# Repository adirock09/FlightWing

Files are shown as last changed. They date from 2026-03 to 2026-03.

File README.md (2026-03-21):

# FlightWing
Screenshot (177)
I made a custom Flight Controller which controls 3 Servos and 1 Escs which is based on an STM32 chip , it has 6 channel input available so it can be connected to a receiver and has a microSD Card, battery charger , IMU and Pressure Sensor . It has a USB-C for uploading code and charging purpose.

## Features

- Based on STM32 Chip
- 2-layer compact PCB
- USB connection for programming and power
- Onboard 3.3V and 5V voltage regulation
- Compact footprint for small projects
- IMU and Pressure Sensor<br>
- 
- ## Bill of Materials (BOM)
| Serial Num | Description | Total (USD) | 
|----:|---|---|
| 1  | PCB and Assembly  |77.86 |
| 2 | Shipping JLCPCB  |14.51 |

<br>
### 💰 Cost Summary

- **Estimated Total Cost ( PCB ASSEMBLY + Shipping):** **$92.37	 USD**
-  ## Schematic & PCB<br>
Screenshot (181)<br>
Screenshot (176)<br>

## 3d Render<br>
Screenshot (177)<br>
Screenshot (178)<br>

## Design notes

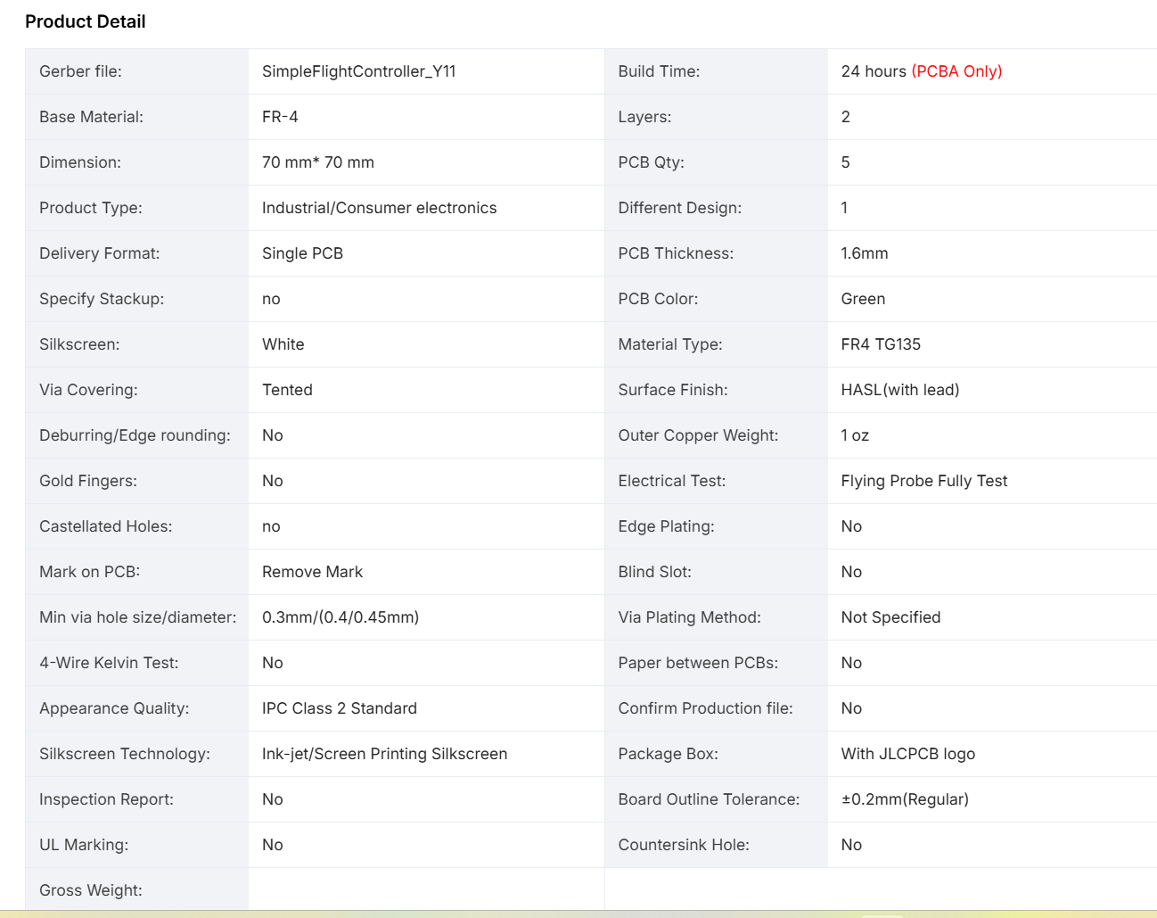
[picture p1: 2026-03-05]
options for PCBA.png

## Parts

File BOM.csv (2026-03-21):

Item | Price | Source
PCB and Assembly | 77.86 | JLCPCB
Shipping JLCPCB | 14.51 | JLCPCB
Total | 92.37 | JLCPCB

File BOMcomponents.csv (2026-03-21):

Designator | Footprint | Quantity | Value | LCSC Part #
BOOT, RESET | SW-SMD_L3.9-W3.0-P4.45 | 2 | TS-1088-AR02016 | C720477
C1, C28, C29, C30 | 0402 | 4 | 1uF
C10, C11, C13 | 0805 | 3 | 22uF
C12, C2, C9 | 0603 | 3 | 10uF
C14, C15, C19, C20, C21, C22, C23, C24, C25, C26, C27, C37 | 0201 | 12 | 100nF
C16 | 0603 | 1 | 2.2uF
C17, C18 | 0402 | 2 | 22uF
C3, C31, C5 | 0402 | 3 | 10uF
C32 | 0201 | 1 | 2.2uF
C33, C34, C35, C36 | 0201 | 4 | 20pF
C4 | 0201 | 1 | 47nF
C6 | 0603 | 1 | 44uF
C7, C8 | 0805 | 2 | 10uF
CARD1 | TF-SMD_TF-01A | 1 | TF-01A | C91145
D1 | 0402 | 1 | LED
J1 | TerminalBlock_Xinya_XY308-2.54-2P_1x02_P2.54mm_Horizontal | 1 | Screw_Terminal_01x02
J2, J3 | PinHeader_1x03_P2.54mm_Vertical | 2 | Conn_01x03
L4 | L0603 | 1 | FCM1608KF-601T03 | C141723
L5 | L2520 | 1 | DFE252012F-1R0M=P2 | C435392
L6 | IND-SMD_L4.0-W4.0-A | 1 | XFL4020-152MEC | C3033018
L7 | IND-SMD_L3.0-W3.0 | 1 | YHNR3015-5R6M | C18236327
R1, R2 | 0201 | 2 | 5.1K
R10, R11, R12, R13, R16, R17, R18, R19, R20, R21, R22, R6, R7, R8, R9 | 0201 | 15 | 10K
R14 | 0402 | 1 | 100K
R15 | 0402 | 1 | 22.1K
R3 | 0201 | 1 | 383
R4 | 0201 | 1 | 5.23K
R5 | 0201 | 1 | 30.1K
U1 | VFQFPN-24_L4.0-W4.0-P0.50-BL-EP2.8 | 1 | BQ25883RGER | C544362
U2 | LGA-14_L3.0-W2.5-P0.50-TL | 1 | ICM-45686 | C22459454
U3 | LQFP-64_10x10mm_P0.5mm | 1 | STM32F722RETx
U4 | LGA-10_L2.0-W2.0-P0.50-TL_BMP580 | 1 | BMP580 | C22391138
U5 | VQFN-HR-15_L3.0-W2.5-P0.50-BL_TPS63070RNMR | 1 | TPS63070RNMR | C109322
U6 | SOT-23-6 | 1 | LMR51430
USB1 | USB-C-SMD_TYPE-C-6PIN-2MD-073 | 1 | TYPE-C 16PIN 2MD(073) | C2765186
X1 | CRYSTAL-SMD_4P-L3.2-W2.5-BL | 1 | X322525MOB4SI | C9006
X2 | FC-135R_L3.2-W1.5 | 1 | Q13FC1350000400 | C32346

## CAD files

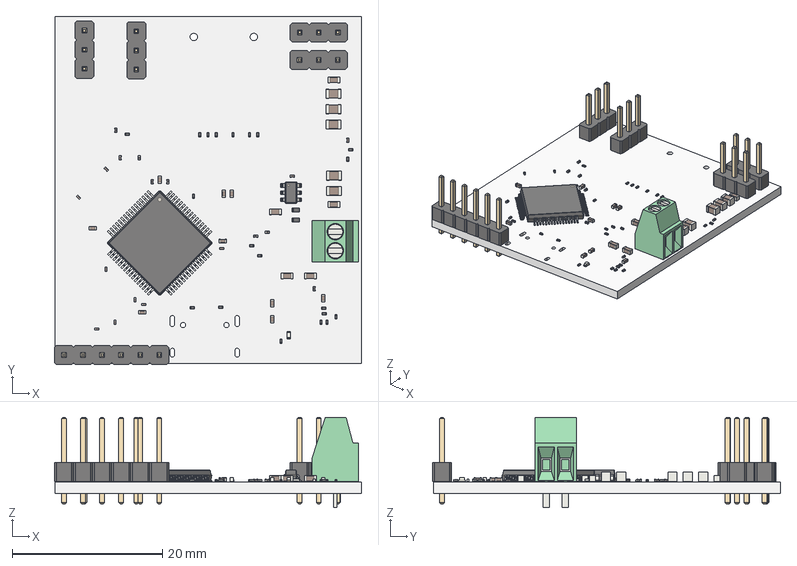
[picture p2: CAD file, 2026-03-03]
FLIGHTWING/CAD/FlightWing.step
40.9 x 46.4 x 12.0 mm
C_0402_1005Metric x 9
C_0201_0603Metric x 18
R_0201_0603Metric x 20
TerminalBlock_Phoenix_MPT-0,5-2-2.54_1x02_P2.54mm_Horizontal
C_0603_1608Metric x 5
C_0805_2012Metric x 5
LED_0402_1005Metric
LQFP-64_10x10mm_P0.5mm
PinHeader_1x03_P2.54mm_Vertical x 4
R_0402_1005Metric x 2
PinHeader_1x06_P2.54mm_Vertical
SOT-23-6
FlightWing_PCB

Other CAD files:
FLIGHTWING/CAD/FlightWing.f3d

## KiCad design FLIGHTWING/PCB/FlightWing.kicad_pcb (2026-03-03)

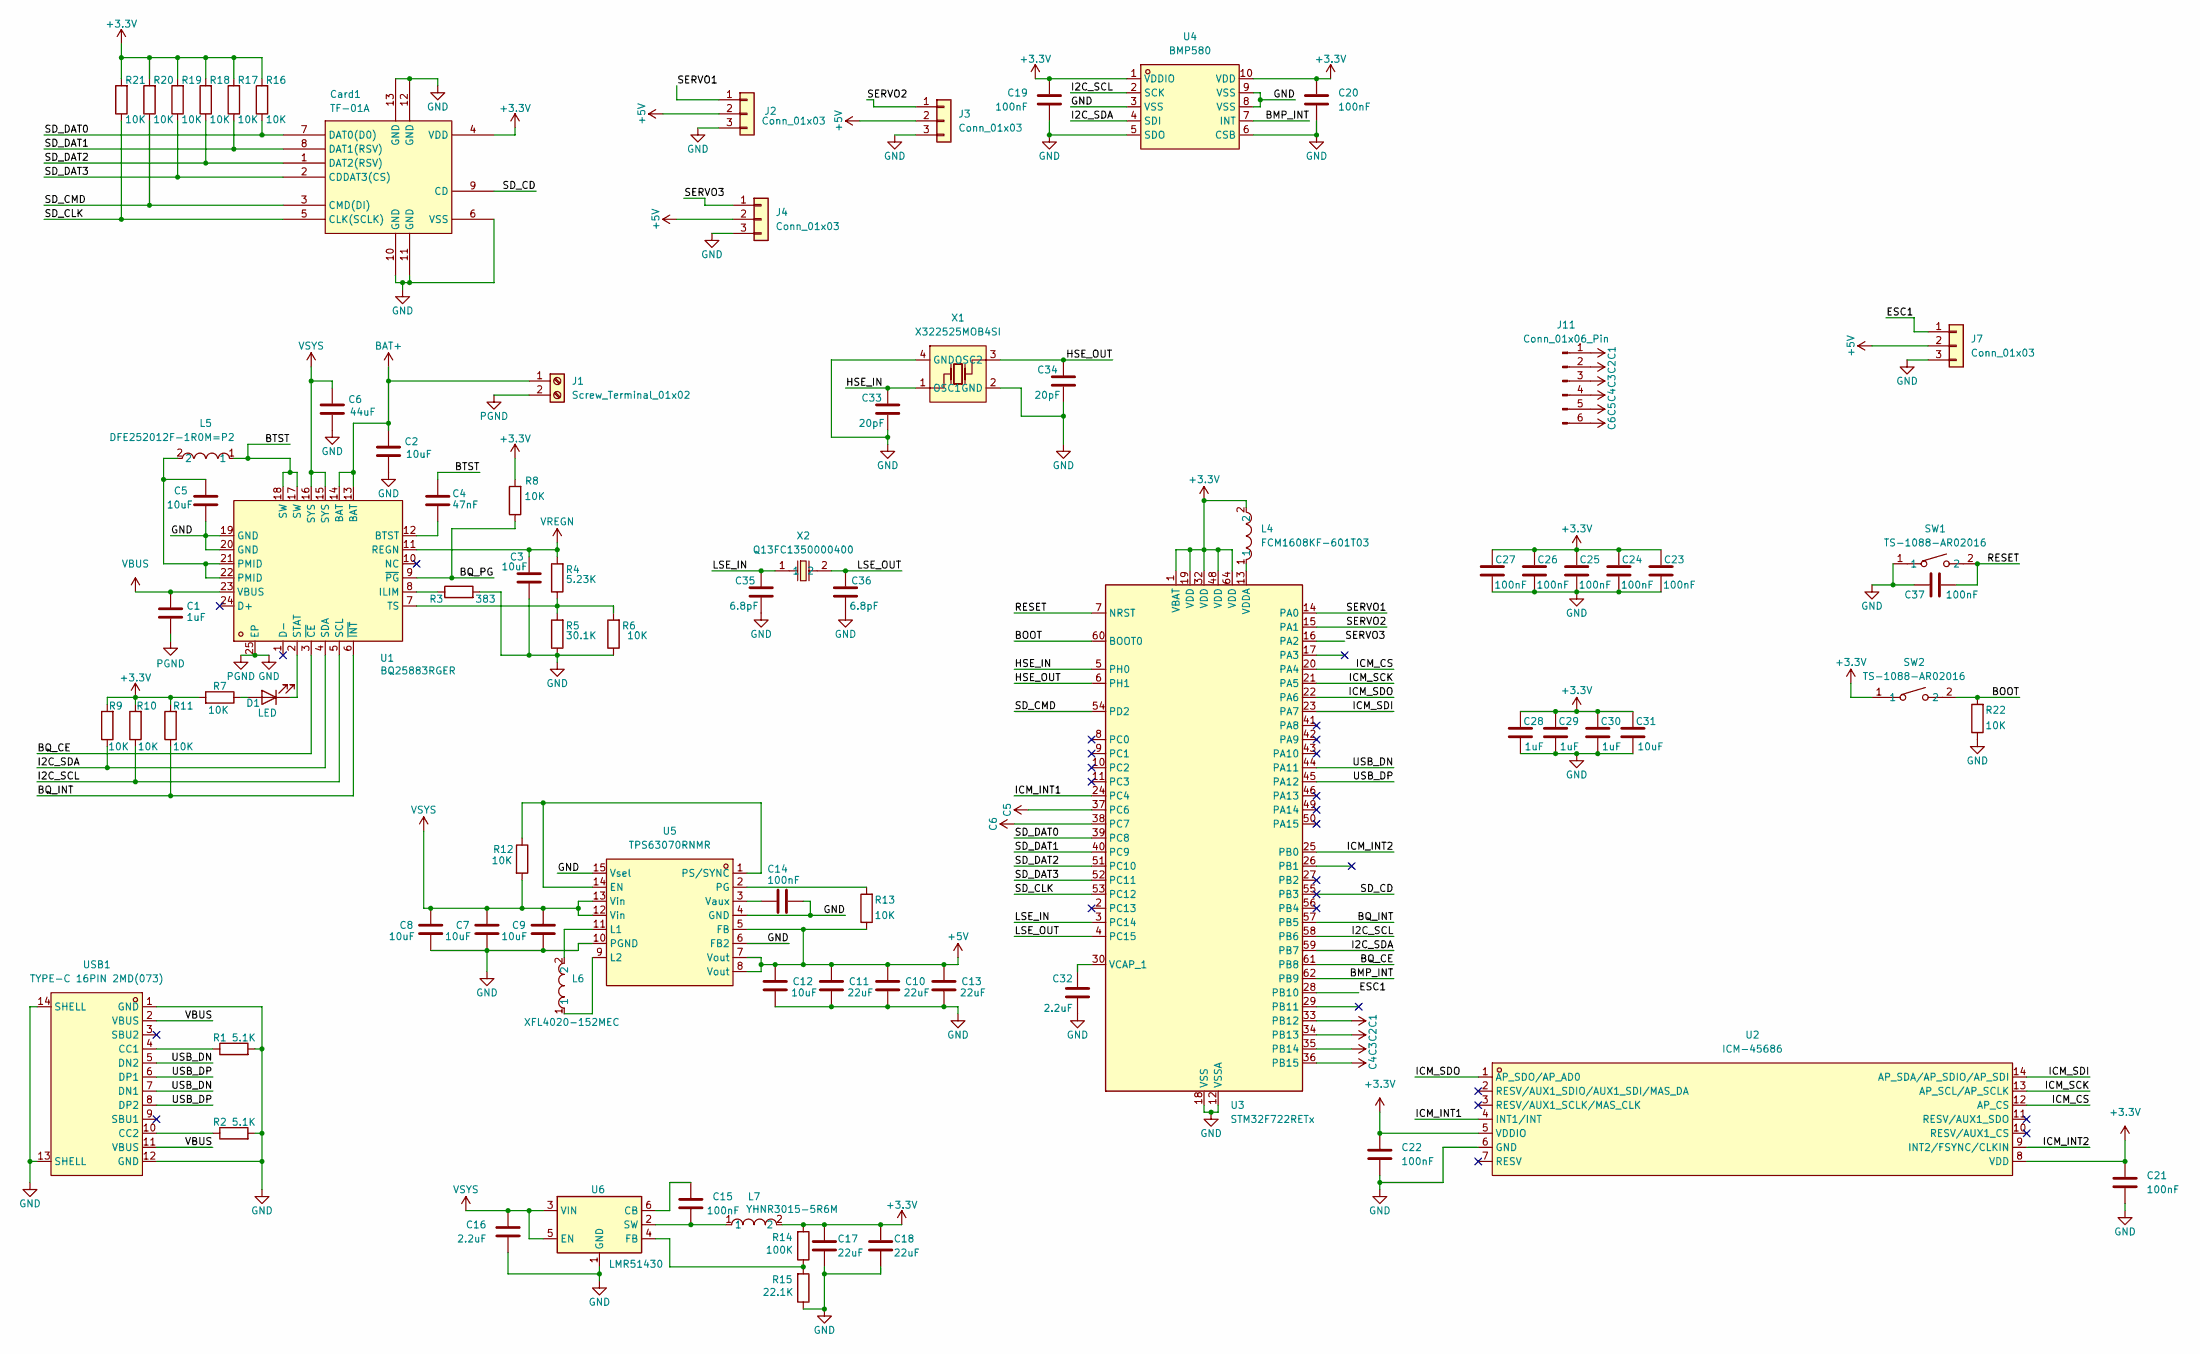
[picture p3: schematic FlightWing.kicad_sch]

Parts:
C1, C28, C29, C30: 1uF; C_0402_1005Metric
C2, C9, C12: 10uF; C_0603_1608Metric
C3, C5, C31: 10uF; C_0402_1005Metric
C4: 47nF; C_0201_0603Metric
C6: 44uF; C_0603_1608Metric
C7, C8: 10uF; C_0805_2012Metric
C10, C11, C13: 22uF; C_0805_2012Metric
C14, C15, C19, C20, C21, C22, C23, C24, C25, C26, C27, C37: 100nF; C_0201_0603Metric
C16: 2.2uF; C_0603_1608Metric
C17, C18: 22uF; C_0402_1005Metric
C32: 2.2uF; C_0201_0603Metric
C33, C34: 20pF; C_0201_0603Metric
C35, C36: 6.8pF; C_0201_0603Metric
Card1: TF-01A; TF-SMD_TF-01A; LCSC Part C91145
D1: LED; LED_0402_1005Metric
J1: Screw_Terminal_01x02; TerminalBlock_Xinya_XY308-2.54-2P_1x02_P2.54mm_Horizontal
J2, J3, J4, J7: Conn_01x03; PinHeader_1x03_P2.54mm_Vertical
J11: Conn_01x06_Pin; PinHeader_1x06_P2.54mm_Vertical
L4: FCM1608KF-601T03; L0603; LCSC Part C141723
L5: DFE252012F-1R0M=P2; L2520; LCSC Part C435392
L6: XFL4020-152MEC; IND-SMD_L4.0-W4.0-A; LCSC Part C3033018
L7: YHNR3015-5R6M; IND-SMD_L3.0-W3.0; LCSC Part C18236327
R1, R2: 5.1K; R_0201_0603Metric
R3: 383; R_0201_0603Metric
R4: 5.23K; R_0201_0603Metric
R5: 30.1K; R_0201_0603Metric
R6, R7, R8, R9, R10, R11, R12, R13, R16, R17, R18, R19, R20, R21, R22: 10K; R_0201_0603Metric
R14: 100K; R_0402_1005Metric
R15: 22.1K; R_0402_1005Metric
SW1, SW2: TS-1088-AR02016; SW-SMD_L3.9-W3.0-P4.45; LCSC Part C720477
U1: BQ25883RGER; VFQFPN-24_L4.0-W4.0-P0.50-BL-EP2.8; LCSC Part C544362
U2: ICM-45686; LGA-14_L3.0-W2.5-P0.50-TL; LCSC Part C22459454
U3: STM32F722RETx; LQFP-64_10x10mm_P0.5mm
U4: BMP580; LGA-10_L2.0-W2.0-P0.50-TL_BMP580; LCSC Part C22391138
U5: TPS63070RNMR; VQFN-HR-15_L3.0-W2.5-P0.50-BL_TPS63070RNMR; LCSC Part C109322
U6: LMR51430; SOT-23-6
USB1: TYPE-C 16PIN 2MD(073); USB-C-SMD_TYPE-C-6PIN-2MD-073; LCSC Part C2765186
X1: X322525MOB4SI; CRYSTAL-SMD_4P-L3.2-W2.5-BL; LCSC Part C9006
X2: Q13FC1350000400; FC-135R_L3.2-W1.5; LCSC Part C32346

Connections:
+3.3V: C17.1, C18.1, C19.1, C20.1, C21.1, C22.1, C23.1, C24.1, C25.1, C26.1, C27.1, C28.1, C29.1, C30.1, C31.1, Card1.4 (VDD), L4.2, L7.2, R7.2, R8.2, R9.2, R10.2, R11.2, R14.2, R16.2, R17.2, R18.2, R19.2, R20.2, R21.2, SW2.1, U2.5 (VDDIO), U2.8 (VDD), U3.1 (VBAT), U3.19 (VDD), U3.32 (VDD), U3.48 (VDD), U3.64 (VDD), U4.1 (VDDIO), U4.10 (VDD)
+5V: C10.1, C11.1, C12.1, C13.1, J2.2, J3.2, J4.2, J7.2, R13.1, U5.5 (FB), U5.7 (Vout), U5.8 (Vout)
/BMP_INT: U3.62 (PB9), U4.7 (INT)
/BOOT: R22.2, SW2.2, U3.60 (BOOT0)
/BQ_CE: U1.3 (~CE), U3.61 (PB8)
/BQ_INT: R11.1, U1.6 (~INT), U3.57 (PB5)
/BQ_PG: R8.1, U1.9 (~PG)
/BTST: C4.1, L5.1, U1.17 (SW), U1.18 (SW)
/ESC1: J7.1, U3.28 (PB10)
/HSE_IN: C33.1, U3.5 (PH0), X1.1 (OSC1)
/HSE_OUT: C34.1, U3.6 (PH1), X1.3 (OSC2)
/I2C_SCL: R10.1, U1.5 (SCL), U3.58 (PB6), U4.2 (SCK)
/I2C_SDA: R9.1, U1.4 (SDA), U3.59 (PB7), U4.4 (SDI)
/ICM_CS: U2.12 (AP_CS), U3.20 (PA4)
/ICM_INT1: U2.4 (INT1/INT), U3.24 (PC4)
/ICM_INT2: U2.9 (INT2/FSYNC/CLKIN), U3.25 (PB0)
/ICM_SCK: U2.13 (AP_SCL/AP_SCLK), U3.21 (PA5)
/ICM_SDI: U2.14 (AP_SDA/AP_SDIO/AP_SDI), U3.23 (PA7)
/ICM_SDO: U2.1 (AP_SDO/AP_AD0), U3.22 (PA6)
/LSE_IN: C35.1, U3.3 (PC14), X2.1
/LSE_OUT: C36.1, U3.4 (PC15), X2.2
/RESET: C37.2, SW1.2, U3.7 (NRST)
/SD_CD: Card1.9 (CD), U3.55 (PB3)
/SD_CLK: Card1.5 (CLK(SCLK)), R21.1, U3.53 (PC12)
/SD_CMD: Card1.3 (CMD(DI)), R20.1, U3.54 (PD2)
/SD_DAT0: Card1.7 (DAT0(D0)), R16.1, U3.39 (PC8)
/SD_DAT1: Card1.8 (DAT1(RSV)), R17.1, U3.40 (PC9)
/SD_DAT2: Card1.1 (DAT2(RSV)), R18.1, U3.51 (PC10)
/SD_DAT3: Card1.2 (CDDAT3(CS)), R19.1, U3.52 (PC11)
/SERVO1: J2.1, U3.14 (PA0)
/SERVO2: J3.1, U3.15 (PA1)
/SERVO3: J4.1, U3.16 (PA2)
/USB_DN: U3.44 (PA11), USB1.5 (DN2), USB1.7 (DN1)
/USB_DP: U3.45 (PA12), USB1.6 (DP1), USB1.8 (DP2)
BAT+: C2.1, J1.1, U1.13 (BAT), U1.14 (BAT)
C1: J11.1, U3.33 (PB12)
C2: J11.2, U3.34 (PB13)
C3: J11.3, U3.35 (PB14)
C4: J11.4, U3.36 (PB15)
C5: J11.5, U3.37 (PC6)
C6: J11.6, U3.38 (PC7)
GND: C1.2, C2.2, C3.2, C5.2, C6.2, C7.2, C8.2, C9.2, C10.2, C11.2, C12.2, C13.2, C14.2, C16.2, C17.2, C18.2, C19.2, C20.2, C21.2, C22.2, C23.2, C24.2, C25.2, C26.2, C27.2, C28.2, C29.2, C30.2, C31.2, C32.2, C33.2, C34.2, C35.2, C36.2, C37.1, Card1.6 (VSS), Card1.10 (GND), Card1.11 (GND), Card1.12 (GND), Card1.13 (GND), J1.2, J2.3, J3.3, J4.3, J7.3, R1.2, R2.2, R3.2, R5.1, R6.1, R15.1, R22.1, SW1.1, U1.19 (GND), U1.20 (GND), U1.25 (EP), U2.6 (GND), U3.12 (VSSA), U3.18 (VSS), U3.31 (VSS), U3.47 (VSS), U3.63 (VSS), U4.3 (VSS), U4.5 (SDO), U4.6 (CSB), U4.8 (VSS), U4.9 (VSS), U5.4 (GND), U5.6 (FB2), U5.10 (PGND), U5.15 (Vsel), U6.1 (GND), USB1.1 (GND), USB1.12 (GND), USB1.13 (SHELL), USB1.14 (SHELL), X1.2 (GND), X1.4 (GND)
unnamed: C5.1, L5.2, U1.21 (PMID), U1.22 (PMID)
unnamed: D1.2 (A), R7.1
unnamed: D1.1 (K), U1.2 (STAT)
unnamed: C4.2, U1.12 (BTST)
unnamed: R3.1, U1.8 (ILIM)
unnamed: R4.1, R5.2, R6.2, U1.7 (TS)
unnamed: C32.1, U3.30 (VCAP_1)
unnamed: L4.1, U3.13 (VDDA)
unnamed: R12.1, U5.1 (PS/SYNC), U5.14 (EN)
unnamed: L6.2, U5.11 (L1)
unnamed: L6.1, U5.9 (L2)
unnamed: R13.2, U5.2 (PG)
unnamed: C14.1, U5.3 (Vaux)
unnamed: C15.1, U6.6 (CB)
unnamed: R14.1, R15.2, U6.4 (FB)
unnamed: C15.2, L7.1, U6.2 (SW)
unnamed: R1.1, USB1.4 (CC1)
unnamed: R2.1, USB1.10 (CC2)
VBUS: C1.1, U1.23 (VBUS), USB1.2 (VBUS), USB1.11 (VBUS)
VREGN: C3.1, R4.2, U1.11 (REGN)
VSYS: C6.1, C7.1, C8.1, C9.1, C16.1, R12.2, U1.15 (SYS), U1.16 (SYS), U5.12 (Vin), U5.13 (Vin), U6.3 (VIN), U6.5 (EN)

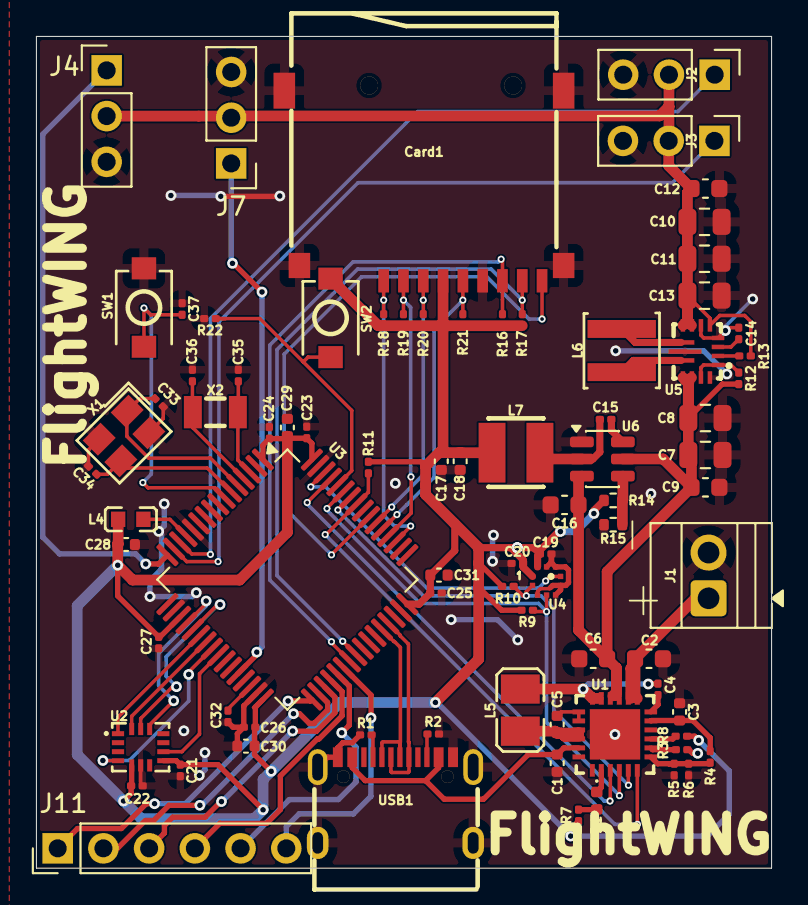
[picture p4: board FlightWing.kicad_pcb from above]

Board: 2 copper layers, 40.8 x 46.2 mm, 82 parts (0 on the bottom side), 63 nets.

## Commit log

2026-03-05 Rename Screenshot (203).png to options for PCBA
2026-03-05 Rename options for PCBA to options for PCBA.png
